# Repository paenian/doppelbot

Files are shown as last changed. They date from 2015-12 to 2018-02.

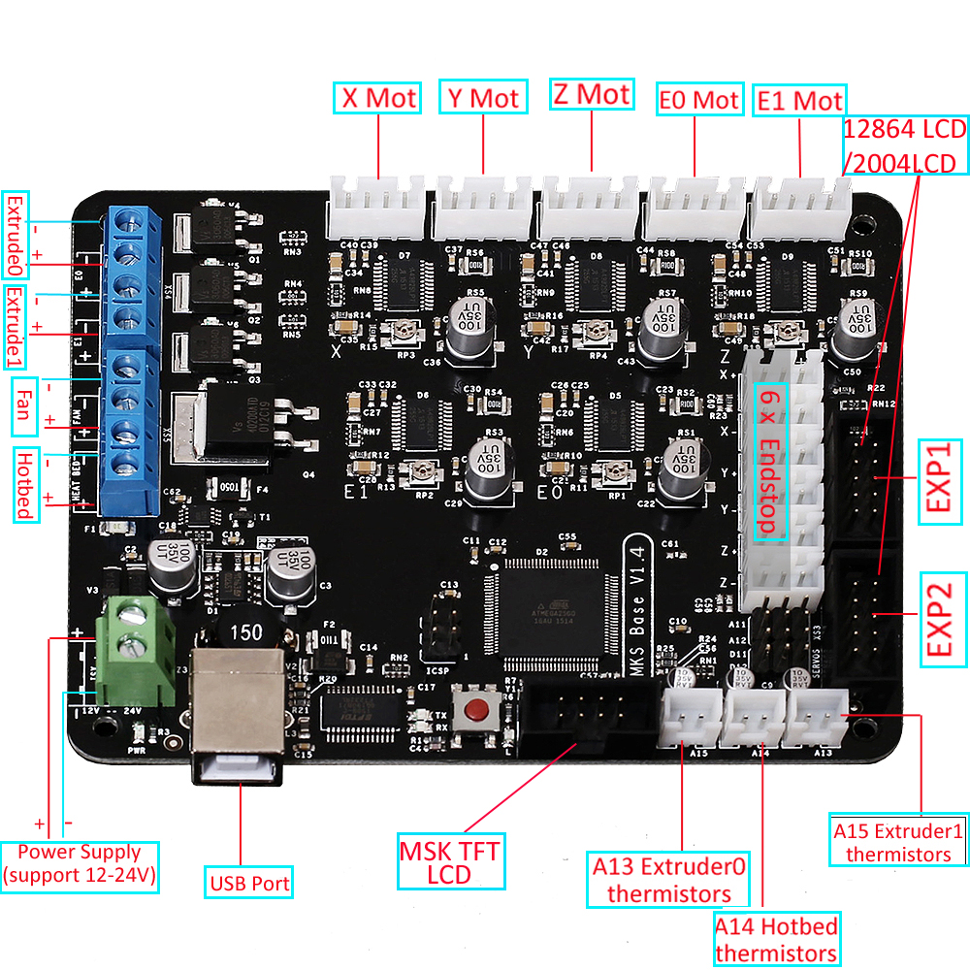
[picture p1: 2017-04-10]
unrelated/mks_base_schematic.jpg

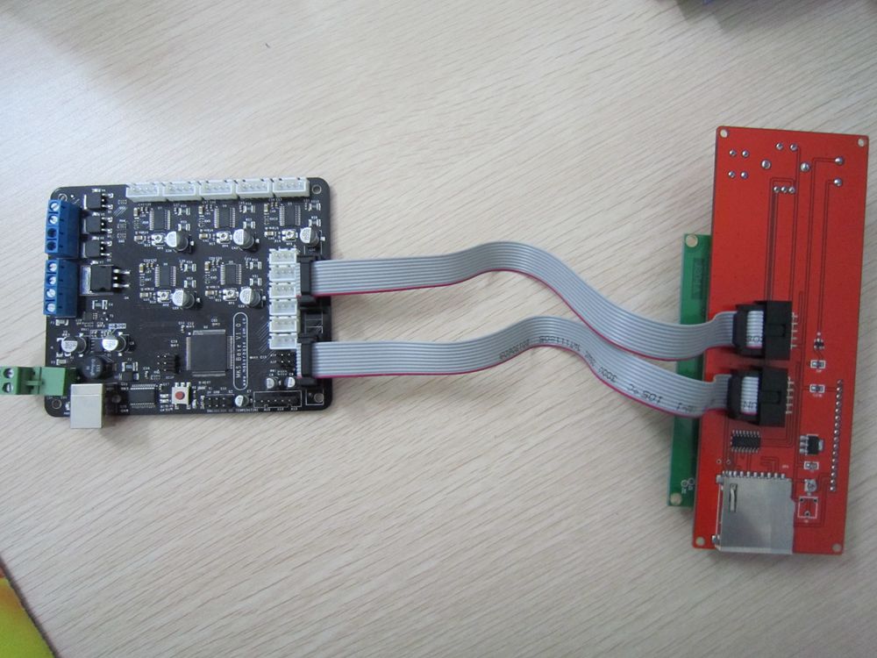
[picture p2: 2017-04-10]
unrelated/mks_base_lcd.jpg

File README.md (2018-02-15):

# doppelbot
Because I like designing 3d printers.

I made a deltabot, and it's really cool.  I can print really tall things.

But 3d prints are weakest in Z - printing really tall is maximizing the weak axis.

So instead of maximizing Z, I though about maximizing Y.  First concept here is the DoppelBot, which is a cube-shaped reprap that's easy to enclose, and has, by default, a one cubic foot build area. the print area of a standard reprap.  It accomplishes this 'twice as big' by the simple expedient of using two heated beds.

The basic design uses two lasercut endcaps, joined by OpenBuilds V-Rail.  The lasercut endcaps ensure that your rails are perfectly perpendicular and parallel - they don't even need to be cut to the exact correct length.  The machine itself uses a CoreXY gantry, and a Z bed with 3 independent leadscrews - so that the bed can truly level itself, none of this bed-level-compensation, if your bed is flat this machine will be able to tram it.

I'm experimenting with 9mm belts and over-built 3d printed carriages, to increase rigidity.

Also experimenting with a continous build system, wherein you can print dozens of objects in a row without human intervention.

Doppelbot running its first print
Picture of the Doppelbot Doppelbot!

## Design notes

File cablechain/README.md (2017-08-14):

# Cable Chain

Designed by Claghorn, this is a great printable cable chain for the Doppelbot.
https://www.thingiverse.com/thing:611593

You need 31 links, and two ends - probably make some custom ends eventually.

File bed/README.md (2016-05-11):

# doppelbot - Bed

## Frame
The bed is made of 2020 V-rail, although the V isn't used so feel free to use regular old 2020 extrusion.  In fact, that might be the default... it needs to be precisely cut, so you could simply order the exact lengths of 2020 from Misumi.

The beams will be joined by MDF endcaps, with MDF braces along the length.  The braces hold the beams square and true, as well as support the bed surface.  

The bed surface is borosilicate glass, a 1' by 2' piece.  Underneath that are two silicone heaters, and underneath those lie a sheet of welding blanket.  Securing the glass surface in place is done with binder clips - I know, it's not elegant, but they're cheap and effective.

It might be a good idea to add a thin piece of aluminum as a heat spreader... I'll certainly be looking into that.  Wondering if aluminum flashing would do it.

## Mechanical
The bed mechanics consist of three leadscrews secured on the end panels; two on the left (where the electronics et al live) and one on the left.  Eventually I would like to use one stepper driver per screw, to support true bed leveling; right now, though, they're just going to be linked to a single Z driver.

##MDF Parts
 - Encap: two needed
  - bed_end_top
  - bed_inside
  - bed_outside
 - Brace: two needed
  - bed_brace_top
  - 2 * bed_inside

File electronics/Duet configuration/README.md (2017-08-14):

# Duet Wifi Configuration!

This is the contents of my Duet Wifi SD card - it contains the latest non-beta firmware, 1.18.1, as well as the latest server, web control and wifi firmwares.
Firmware comes from here: https://github.com/dc42/RepRapFirmware/tree/dev/Release/Duet-WiFi/Stable
The rest of that GitHub is development et al - those are the latest stable bits.

## Firmwares
To update, copy this to your Duet Wifi SD card - as long as you have a working Duet Wifi firmware, it can update itself!

You need these four files in the /sys/ folder on your SD card:
DuetWebControl-1.15a.bin	Version 1.18	4 months ago
DuetWiFiFirmware-1.18.1.bin	Version 1.18.1	4 months ago
DuetWiFiServer-1.03-ch.bin	Version 1.16 release	9 months ago
iap4e.bin

Then you can run "M997 S0:1:2" to update all of them at once.
https://duet3d.com/wiki/Updating_more_than_one_firmware_at_a_time

## Config
Also in the /sys/ folder are the config files - here's a quick rundown.

All the configuration is done in gcode - so if you want to test a new config, simply send the gcode; if it works as you intended, you can then write it into the appropriate file.
Gcodes are documented here: http://reprap.org/wiki/Gcode
You MUST pay attention to the "supported by RepRapFirmware" box!

config.g - most of the parameters to set up the machine - steps per mm, extruder settings, endstops, etc.
homeall.g - what to do when G28 is called
home[xyz].g - what to do when G28 [XYZ] is called
pause.g - how to pause
resume.g - how to resume

I haven't looked at the rest of the .g files yet.

## Macros
I, uh, just copied these over.

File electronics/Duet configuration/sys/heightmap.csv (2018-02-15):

RepRapFirmware height map file v2 generated at 2018-00-27 00:49 | mean error 0.047 | deviation 0.098
xmin | xmax | ymin | ymax | radius | xspacing | yspacing | xnum | ynum
50.00 | 250.00 | 50.00 | 250.00 | -1.00 | 50.00 | 50.00 | 5 | 5
-0.064 | -0.031 | -0.071 | -0.072 | -0.061
0.036 | 0.132 | -0.082 | -0.001 | -0.007
0.069 | 0.301 | 0.227 | -0.106 | 0.054
0.110 | 0.147 | 0.064 | 0.087 | 0.021
0.150 | 0.064 | 0.016 | 0.079 | 0.113

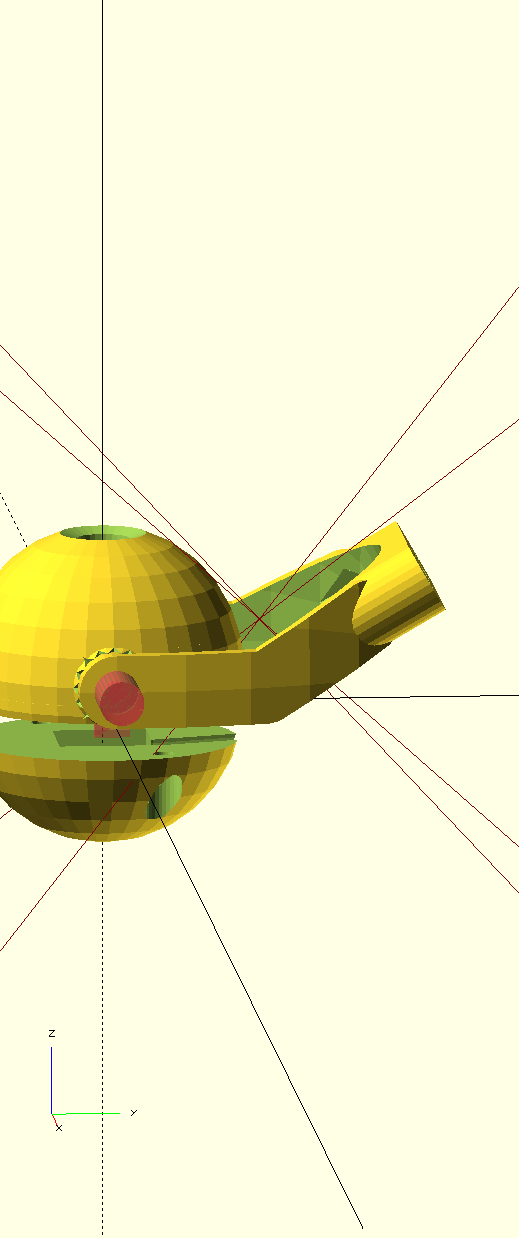
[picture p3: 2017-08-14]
unrelated/gurmeet/base_30.png

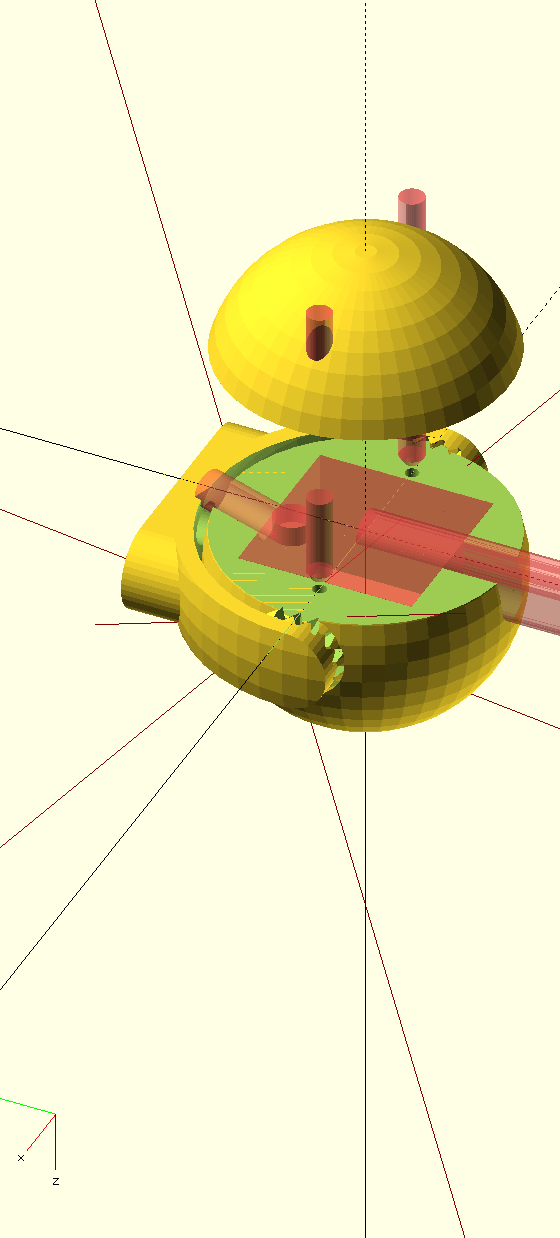
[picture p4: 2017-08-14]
unrelated/gurmeet/rear_view.png

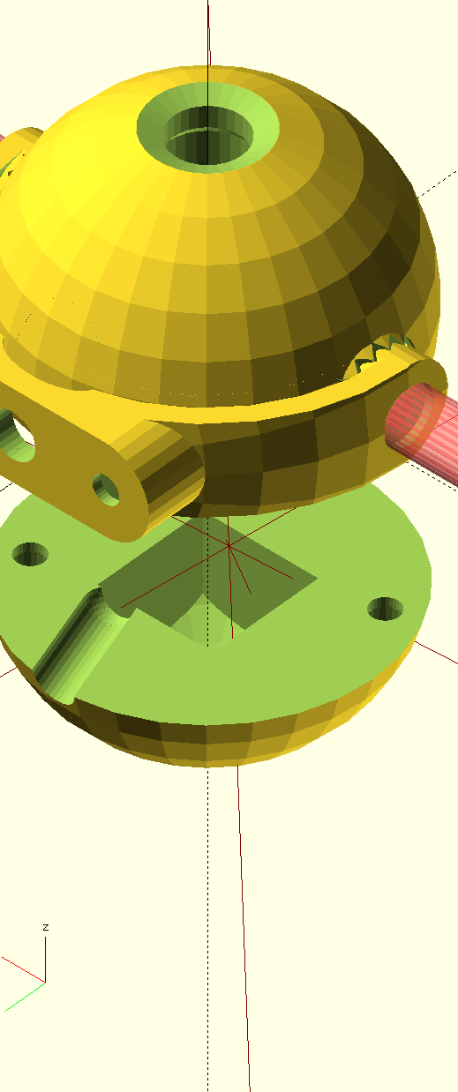
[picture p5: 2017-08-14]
unrelated/gurmeet/hole_pic.png

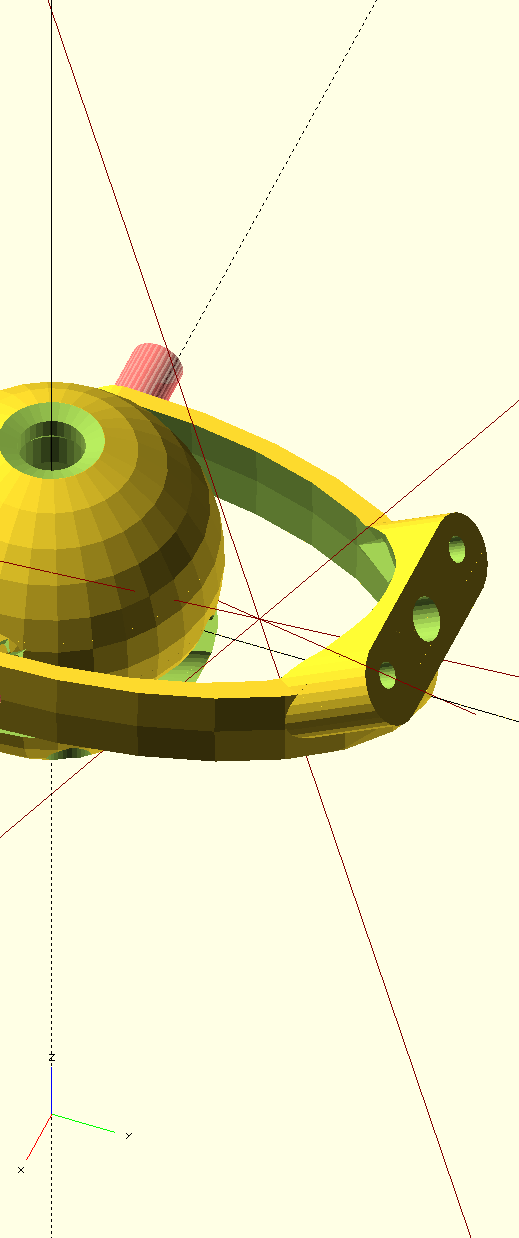
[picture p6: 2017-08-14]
unrelated/gurmeet/base_angle.png

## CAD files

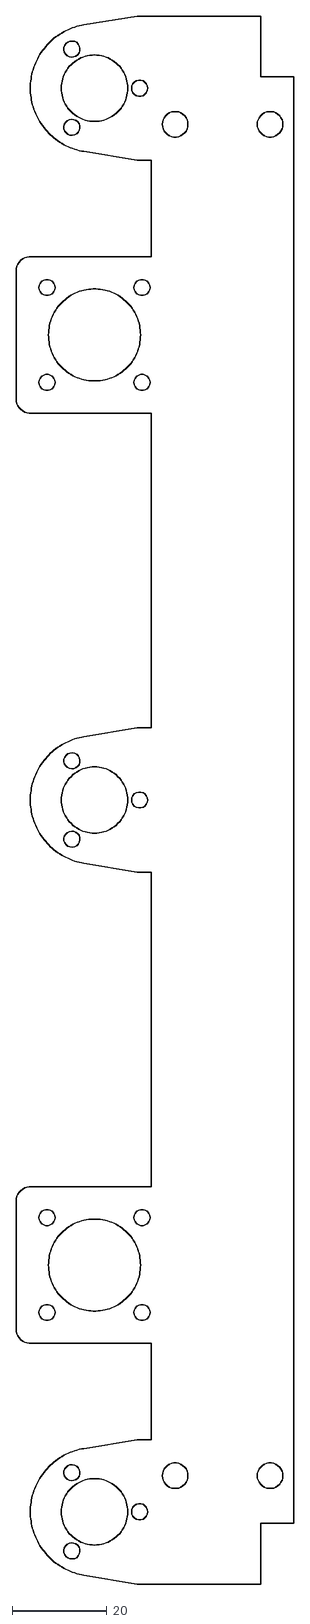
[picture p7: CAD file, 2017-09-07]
bed/dxf/bed_thick_top.dxf
58.5 x 330.4

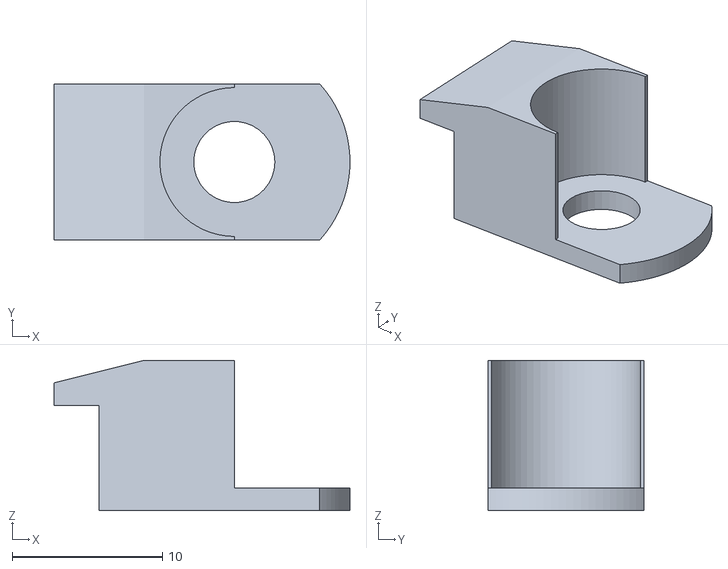
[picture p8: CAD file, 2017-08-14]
bed/stl/bed_clamp.stl
19.7 x 10.4 x 10.0

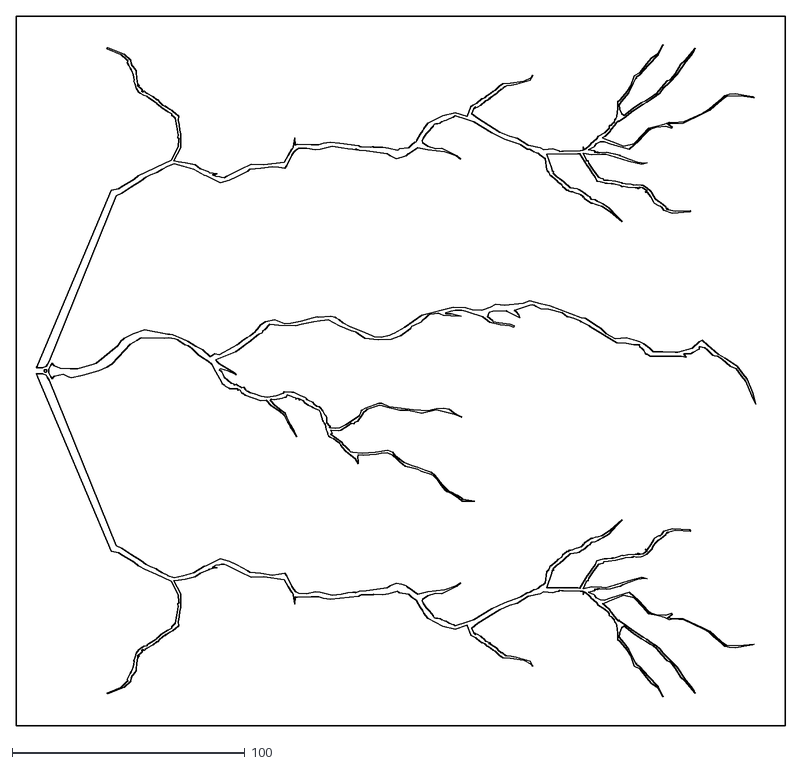
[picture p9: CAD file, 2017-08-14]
bed/vacuum_lightning.dxf
330.2 x 304.8

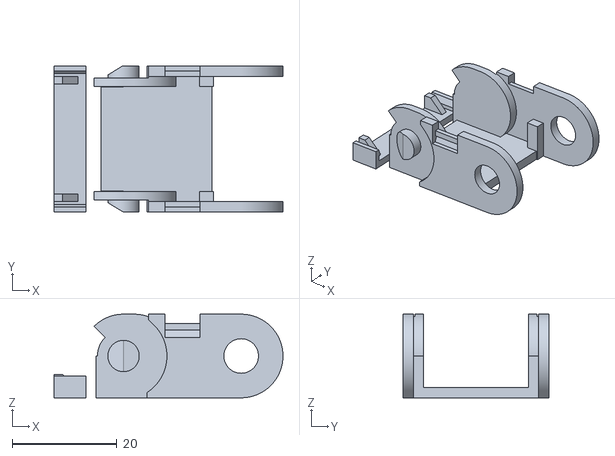
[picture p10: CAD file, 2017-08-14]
cablechain/schleppkette_thingiverse.stl
43.8 x 28.0 x 16.0

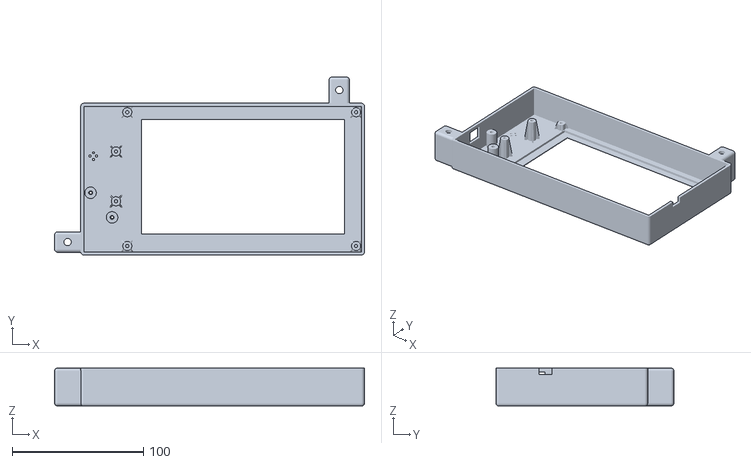
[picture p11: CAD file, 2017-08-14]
electronics/PanelDueEnclosure.stl
236.4 x 135.8 x 29.0

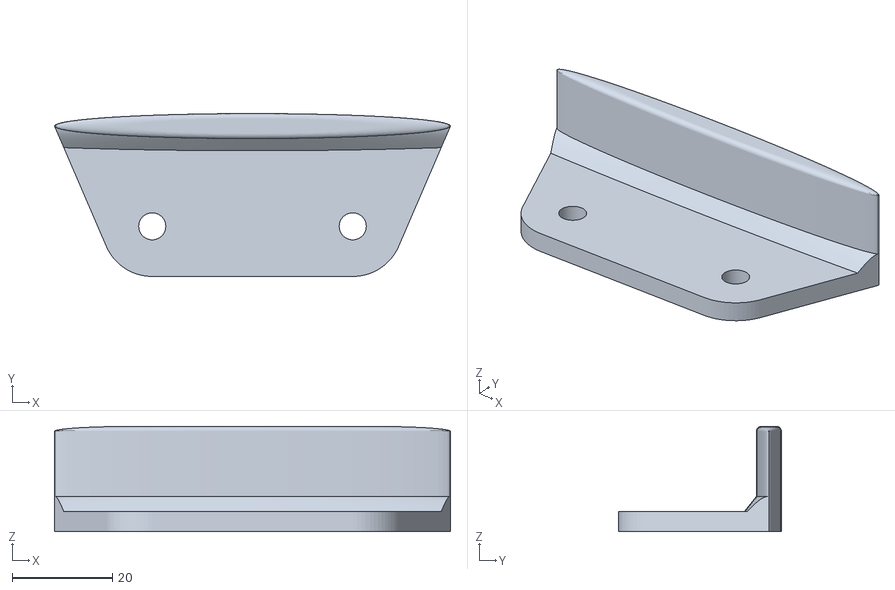
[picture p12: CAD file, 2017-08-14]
endcap/belt_separator.stl
79.0 x 32.5 x 21.0

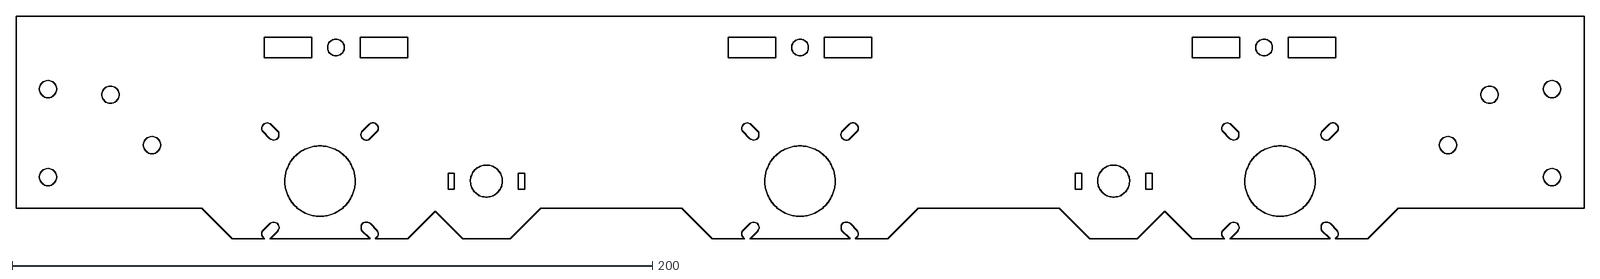
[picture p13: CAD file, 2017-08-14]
endcap/dxf/top_wall_plate_idler.dxf
490.0 x 69.5

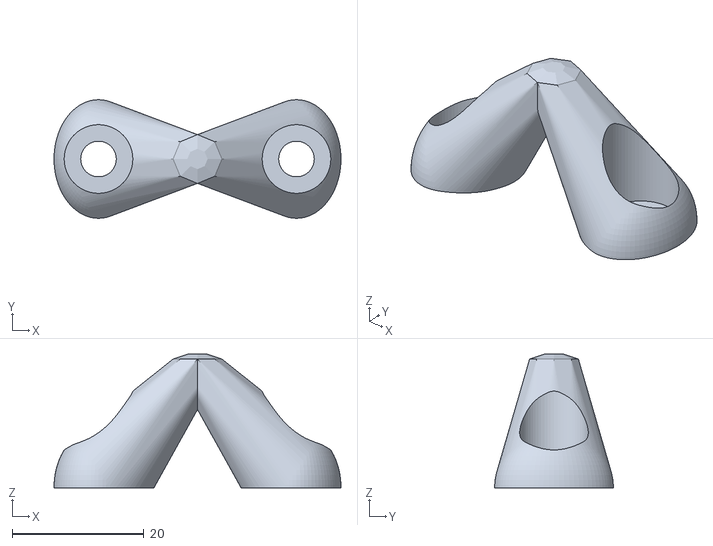
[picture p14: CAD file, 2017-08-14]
extras/feet.stl
43.5 x 18.0 x 20.2

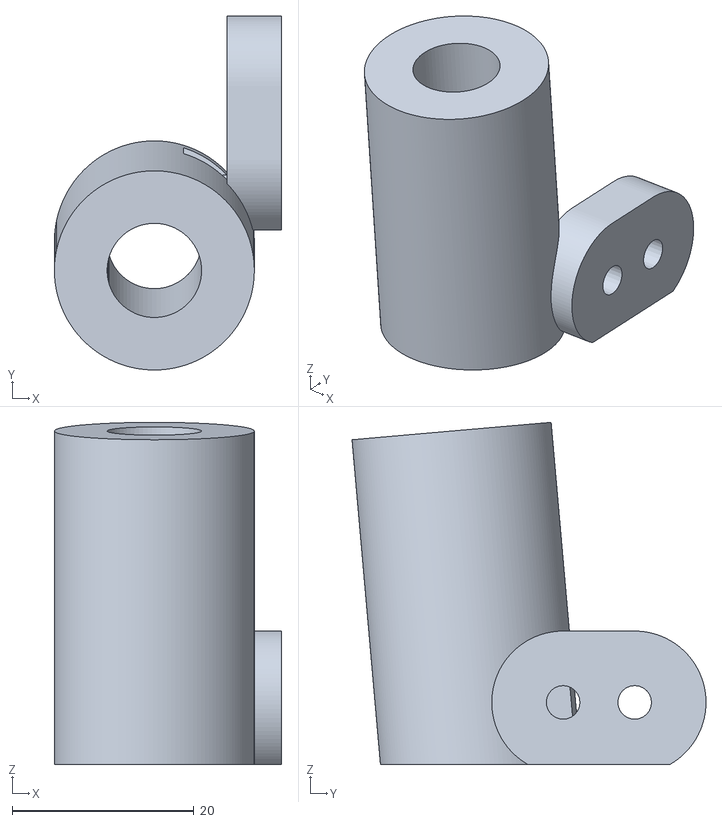
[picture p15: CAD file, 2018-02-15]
extruder/cablechain_mount.stl
25.0 x 39.0 x 37.7

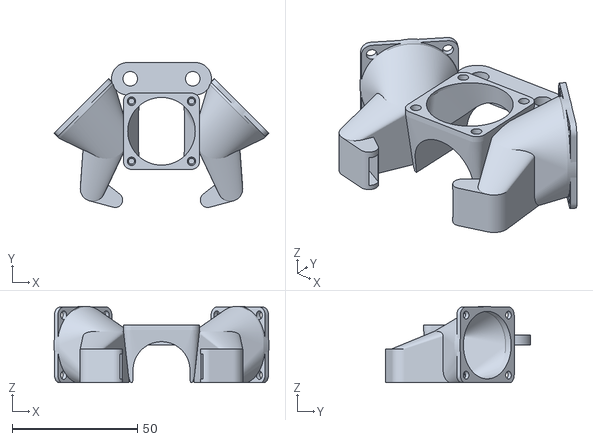
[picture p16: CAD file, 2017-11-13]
extruder/stl/cooling_fan_duct.stl
86.0 x 58.0 x 30.5

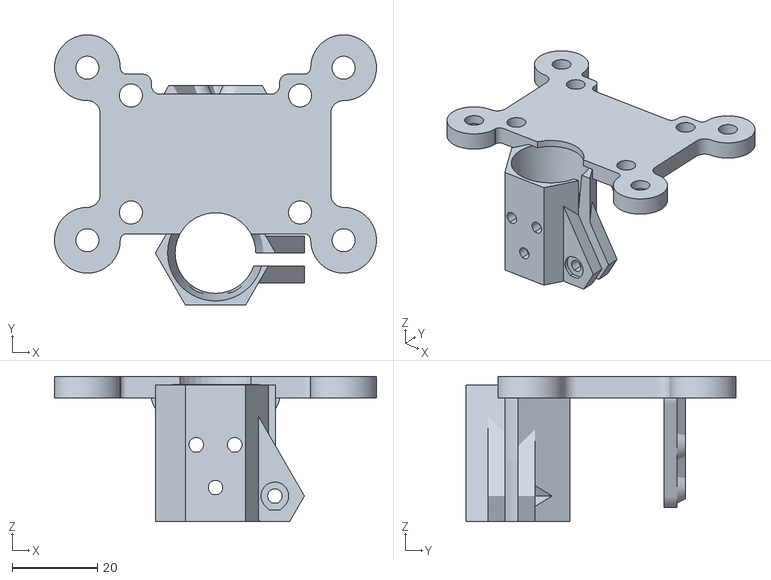
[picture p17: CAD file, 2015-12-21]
gantry.stl
75.4 x 63.3 x 34.0

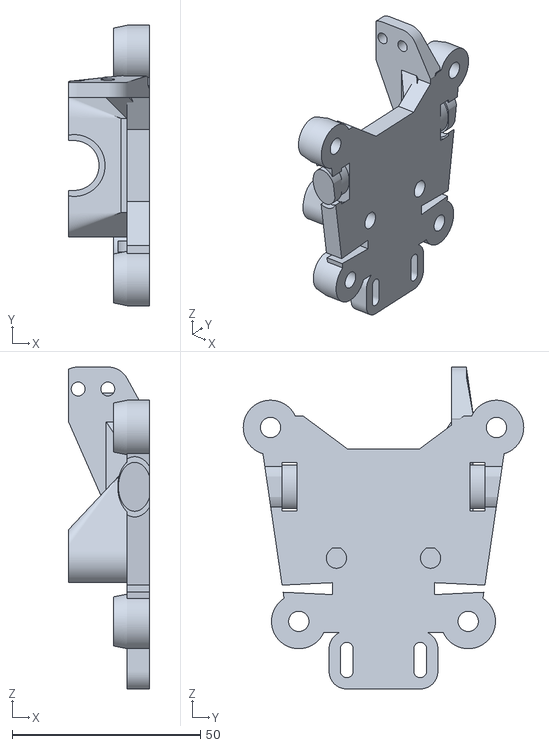
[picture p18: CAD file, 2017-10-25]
gantry/bowden_carriage.stl
21.5 x 74.5 x 85.5

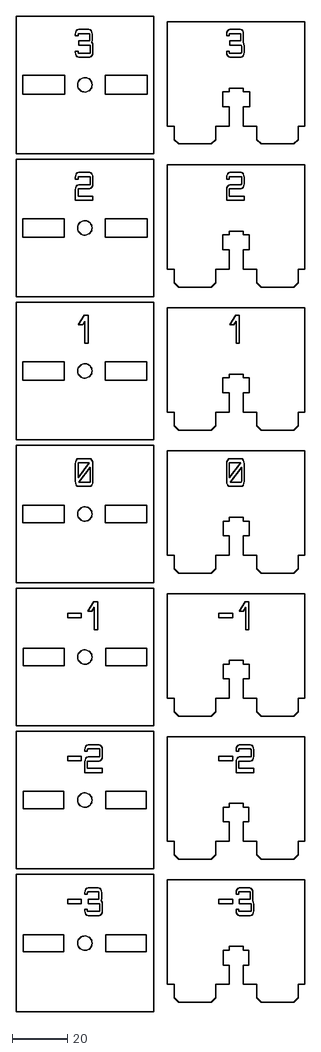
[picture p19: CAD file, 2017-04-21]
laser_testing/test_array.dxf
105.0 x 362.0

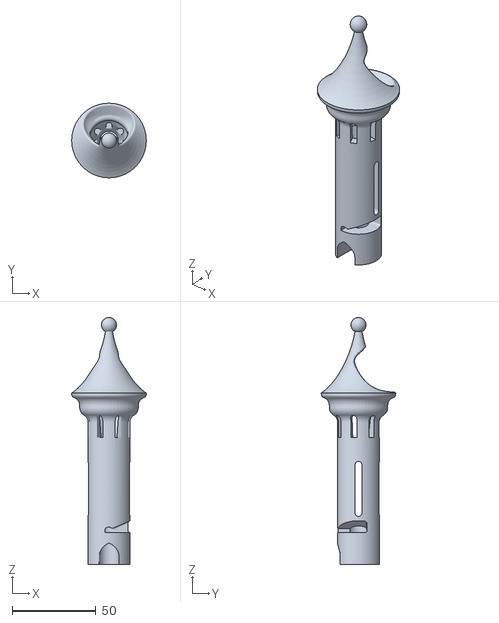
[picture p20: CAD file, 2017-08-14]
unrelated/castle_game/files-turm-klein.stl
44.6 x 44.6 x 147.6

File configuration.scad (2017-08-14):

in = 25.4;
mdf_wall = 6.5;
mdf_tab = 15;

wall = 5;

screw_slop = .2;
slop = .2;
laser_slop = -.1;

smooth_rod_rad = 10/2+laser_slop+.1;
smooth_rod_sep =490/5;

//this is for the old printer 
//smooth_rod_sep = 115;

//these can't change - measured values.
beam = 20;
bed_screw_sep = 309;
bed = 300;

layer_height=.2;

//this is using the gt2 idlers from robotdigg
//idler_rad = 13/2;
//idler_flange_rad = 18/2;
//idler_thick = 12;

//these use the smaller M5 flanged bearings as idlers
idler_rad = 16/2;
idler_flange_rad = 18/2;
idler_thick = 11.5;

//flanged bearing for the Z idler
z_bearing=22/2;
z_bearing_flange = 25/2;
leadscrew_rad = 8/2+slop;
leadscrew_shaft_rad = 7;
leadscrew_screw_rad = 19.05/2;

pulley_rad = 13/2;
pulley_flange_rad = 18/2;

//using the mini V-wheels
wheel_rad = 15.5/2;
wheel_inner_rad = 12.5/2;
wheel_clearance = 18;
wheel_height = 9;
wheel_inner_height = 5;
wheel_flange_rad = 16/2;

eccentric_rad = 7.3/2;
eccentric_flange_rad = 11/2;

//frame lengths - may be dependent on wall above.
frame_x = 500;  //we lose more in X because of the endcaps - it's where all the motors etc. will hide.
frame_y = 490;  //(490-300)/2-beam=75mm clearance on either side of the print bed.
corner_y = frame_y-75;
frame_z = 440;  //because the leadscrews are short, the motors stick up and the feet stick down
corner_z = frame_z-25;

corner_endplate = true; //this controls wether you want a full endcap, or just the corners.  Corners allows twisting in a direction that should be impossible when the rails are connected on both ends, but I wanted to retain the old option just in case.
corner_length = 170; //length of the corner side support.

foot_height = 25.4;  //extra meat on the legs

echo("BOM: 4, reg rail, 2020", frame_x, "Frame");

belt_thick = 9;
belt_width = 1.5;

//motor size and placement variables
motor_w = 42;
motor_r = 52/2;
motor_y = frame_y/2-beam-pulley_rad-belt_width; //distance motors are from the center.
motor_screw_sep = 31;




//gantry - might want to make it bigger
echo("BOM: 1, v-rail, 2020", frame_y, "Gantry");

//bed lengths
bed_x = 300+beam*2;
bed_y = 300;  //the screwholes on the bed should line up with the long_bed rails.

bed_screw_offset_y = bed_y/2;
bed_screw_offset_x = 15+5+2;

echo("BOM: 2, reg rail, 2020", bed_x, "Bed mount");
echo("BOM: 3, reg rail, 2020", bed_y, "Bed mount");  //might want more than three - to hold insulation well.

//standard screw variables
m3_nut_rad = 6.01/2+slop;
m3_nut_height = 2.4;
m3_rad = 3/2+slop;
m3_cap_rad = 3.25;
m3_cap_height = 2;
m3_sq_nut_rad = 7.9/2;


m4_nut_rad = 7.66/2+slop;
m4_nut_height = 3.2;
m4_rad = 4/2+slop;
m4_cap_rad = 7/2+slop;
m4_cap_height = 2.5;

m5_nut_rad = 8.79/2;
m5_sq_nut_rad = (8*sqrt(2)+slop/2)/2;
m5_nut_rad_laser = 8.79/2-.445;
m5_nut_height = 4.7;
m5_rad = 5/2+slop;
m5_rad_laser = 5/2-.1;
m5_cap_rad = 10/2+slop;
m5_cap_height = 3;
m5_washer_rad = 11/2+slop;


//redoing the frame with 10-24 screws - will use them for self-tapping screws
//on the endcaps, as well as all the MDF->MDF joints.  The reason for this is
//that the nuts on 10-24 are MUCH larger than  M5 nuts - making it way less
//likely to ruin the MDF.
ten24_rad = (.19*in/2+slop);
ten24_cap_rad = (.361*in/2+slop);
ten24_cap_height = .101*in+slop;
ten24_nut_rad = ((3/8*in)*cos(180/6))/2;
ten24_sq_nut_rad = ((3/8*in)*sqrt(2))/2+slop/2;

ten24_nut_height = 1/8*in+slop;

ten24_rad_laser = ten24_rad+laser_slop/2;
ten24_sq_nut_rad_laser = ten24_sq_nut_rad+laser_slop/2;
ten24_sq_nut_flat = 9.5;
ten24_sq_nut_flat_laser = ten24_sq_nut_flat+laser_slop;


echo(m5_sq_nut_rad);
echo(ten24_sq_nut_rad);



//some enums
MALE = 1;
FEMALE = -1;

//makes all the holes have lots of segments
$fs=.5;
$fa=.1;

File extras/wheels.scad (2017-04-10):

slop = .2;

m5_nut_rad = 8.79/2+slop;
m5_nut_height = 4.7;
m5_rad = 5/2+slop;
m5_dia = 5+slop;
m5_cap_rad = 9/2+slop;
m5_washer_rad = 11/2;

wall = 6;

//%cylinder(r=m8_washer_rad,h=20);
//%rotate([90,0,0])translate([-34.5,13,-2]) cylinder(r=m8_rad, h=30, center=true);

//the wheel
translate([-31,T/2,9]) rotate([90,0,0]) //this puts the wheel in the carrier
!wheel();

//the carrier
//rotated for printing
difference(){
	translate([0,0,17.5]) rotate([0,-12,0])
	carrier();
	translate([0,0,-50]) cube([100,100,100], center=true);
    
    translate([0,0,-18]) rotate([0,-24,0])
    translate([0,0,100]) cube([100,100,100], center=true);
}

module carrier(){
    bump_height = 1.5;
    
	thickness = wall+wall+bump_height*2+T;
	difference(){
		union(){
            //extra base clearance
            translate([6.25,0,0]) cube([6.5, 19.5, 39.5], center=true);
            
			hull(){
				cube([wall, thickness, 40], center=true);
				
				translate([-D/2-wall,0,0]) rotate([90,0,0]) cylinder(r=m5_washer_rad+wall, h=thickness, center=true);
			}
		}

		//mount the wheel
		translate([-D/2-wall,0,0]) rotate([-90,0,0]) {
			rotate([0,0,25]) cap_cylinder(r=m5_rad, h=50, center=true);
			difference(){
				scale([1,1.25,1]) intersection(){
					cylinder(r=D/2+wall,h=T+2,center=true,$fn=100);
					scale([1,1,.5]) sphere(r=D/2+wall, $fn=90);
				}
                
				//bumps to hold the wheel centered
				for(i=[0,1]) mirror([0,0,i]) translate([0,0,-T/2-1.1]) cylinder(r1=m5_washer_rad+1, r2=m5_washer_rad-1, h=bump_height);
			}
		}
		
		//bolt indent
		translate([-D/2-wall,0,0])rotate([-90,0,0]) translate([0,0,-T/2-1.05-wall]) cylinder(r=m5_washer_rad+.25, h=2);
		//nut indent
		mirror([0,1,0]) translate([-D/2-wall,0,0])rotate([-90,0,0]) translate([0,0,-T/2-1.05-wall]) cylinder(r=m5_nut_rad+.1, h=2, $fn=6);

		//mount the carrier
		for(i=[-10,10]) translate([0,0,i]) rotate([0,90,0]){
			rotate([0,0,-90]) cap_cylinder(r=m5_rad, h=30, center=true);
			translate([0,0,-30]) rotate([0,0,-90]) cap_cylinder(r=m5_cap_rad+.25, h=35);
		}
	}
}

// outer diameter of ring
D=65;
// thickness
T=18;
// clearance
tol=.3;
number_of_planets=8;
number_of_teeth_on_planets=6;
approximate_number_of_teeth_on_sun=13;
// pressure angle
P=40;//[30:60]
// number of teeth to twist across
nTwist=1;
// width of center hole
w=m5_dia+1  ;

DR=0.5*1;// maximum depth ratio of teeth

m=round(number_of_planets);
np=round(number_of_teeth_on_planets);
ns1=approximate_number_of_teeth_on_sun;
k1=round(2/m*(ns1+np));
k= k1*m%2!=0 ? k1+1 : k1;
ns=k*m/2-np;
echo(ns);
nr=ns+2*np;
pitchD=0.9*D/(1+min(PI/(2*nr*tan(P)),PI*DR/nr));
pitch=pitchD*PI/nr;
echo(pitch);
helix_angle=atan(2*nTwist*pitch/T);
echo(helix_angle);

phi=$t*360/m;
module wheel(){
	translate([0,0,T/2]){
		difference(){
			intersection(){
				cylinder(r=D/2+1,h=T,center=true,$fn=100);
				scale([1,1,1.25]) sphere(r=D/2+1, $fn=90);
			}
			render() herringbone(nr,pitch,P,DR,-tol,helix_angle,T+0.2);
		}
		rotate([0,0,(np+1)*180/ns+phi*(ns+np)*2/ns])
		difference(){
			mirror([0,1,0])
				render() herringbone(ns,pitch,P,DR,tol,helix_angle,T);
			cylinder(r=w/2,h=T+1,center=true);
		}
		for(i=[1:m])rotate([0,0,i*360/m+phi])translate([pitchD/2*(ns+np)/nr,0,0])
			render() rotate([0,0,i*ns/m*360/np-phi*(ns+np)/np-phi])
				herringbone(np,pitch,P,DR,tol,helix_angle,T);
	}
}

module rack(
	number_of_teeth=15,
	circular_pitch=10,
	pressure_angle=28,
	helix_angle=0,
	clearance=0,
	gear_thickness=5,
	flat=false){
addendum=circular_pitch/(4*tan(pressure_angle));

flat_extrude(h=gear_thickness,flat=flat)translate([0,-clearance*cos(pressure_angle)/2])
	union(){
		translate([0,-0.5-addendum])square([number_of_teeth*circular_pitch,1],center=true);
		for(i=[1:number_of_teeth])
			translate([circular_pitch*(i-number_of_teeth/2-0.5),0])
			polygon(points=[[-circular_pitch/2,-addendum],[circular_pitch/2,-addendum],[0,addendum]]);
	}
}

module herringbone(
	number_of_teeth=15,
	circular_pitch=10,
	pressure_angle=28,
	depth_ratio=1,
	clearance=0,
	helix_angle=0,
	gear_thickness=5){
union(){
	gear(number_of_teeth,
		circular_pitch,
		pressure_angle,
		depth_ratio,
		clearance,
		helix_angle,
		gear_thickness/2);
	mirror([0,0,1])
		gear(number_of_teeth,
			circular_pitch,
			pressure_angle,
			depth_ratio,
			clearance,
			helix_angle,
			gear_thickness/2);
}}

module gear (
	number_of_teeth=15,
	circular_pitch=10,
	pressure_angle=28,
	depth_ratio=1,
	clearance=0,
	helix_angle=0,
	gear_thickness=5,
	flat=false){
pitch_radius = number_of_teeth*circular_pitch/(2*PI);
twist=tan(helix_angle)*gear_thickness/pitch_radius*180/PI;

flat_extrude(h=gear_thickness,twist=twist,flat=flat)
	gear2D (
		number_of_teeth,
		circular_pitch,
		pressure_angle,
		depth_ratio,
		clearance);
}

module flat_extrude(h,twist,flat){
	if(flat==false)
		linear_extrude(height=h,twist=twist,slices=twist/6)child(0);
	else
		child(0);
}

module gear2D (
	number_of_teeth,
	circular_pitch,
	pressure_angle,
	depth_ratio,
	clearance){
pitch_radius = number_of_teeth*circular_pitch/(2*PI);
base_radius = pitch_radius*cos(pressure_angle);
depth=circular_pitch/(2*tan(pressure_angle));
outer_radius = clearance<0 ? pitch_radius+depth/2-clearance : pitch_radius+depth/2;
root_radius1 = pitch_radius-depth/2-clearance/2;
root_radius = (clearance<0 && root_radius1<base_radius) ? base_radius : root_radius1;
backlash_angle = clearance/(pitch_radius*cos(pressure_angle)) * 180 / PI;
half_thick_angle = 90/number_of_teeth - backlash_angle/2;
pitch_point = involute (base_radius, involute_intersect_angle (base_radius, pitch_radius));
pitch_angle = atan2 (pitch_point[1], pitch_point[0]);
min_radius = max (base_radius,root_radius);

intersection(){
	rotate(90/number_of_teeth)
		circle($fn=number_of_teeth*3,r=pitch_radius+depth_ratio*circular_pitch/2-clearance/2);
	union(){
		rotate(90/number_of_teeth)
			circle($fn=number_of_teeth*2,r=max(root_radius,pitch_radius-depth_ratio*circular_pitch/2-clearance/2));
		for (i = [1:number_of_teeth])rotate(i*360/number_of_teeth){
			halftooth (
				pitch_angle,
				base_radius,
				min_radius,
				outer_radius,
				half_thick_angle);		
			mirror([0,1])halftooth (
				pitch_angle,
				base_radius,
				min_radius,
				outer_radius,
				half_thick_angle);
		}
	}
}}

module halftooth (
	pitch_angle,
	base_radius,
	min_radius,
	outer_radius,
	half_thick_angle){
index=[0,1,2,3,4,5];
start_angle = max(involute_intersect_angle (base_radius, min_radius)-5,0);
stop_angle = involute_intersect_angle (base_radius, outer_radius);
angle=index*(stop_angle-start_angle)/index[len(index)-1];
p=[[0,0],
	involute(base_radius,angle[0]+start_angle),
	involute(base_radius,angle[1]+start_angle),
	involute(base_radius,angle[2]+start_angle),
	involute(base_radius,angle[3]+start_angle),
	involute(base_radius,angle[4]+start_angle),
	involute(base_radius,angle[5]+start_angle)];

difference(){
	rotate(-pitch_angle-half_thick_angle)polygon(points=p);
	square(2*outer_radius);
}}

// Mathematical Functions
//===============

// Finds the angle of the involute about the base radius at the given distance (radius) from it's center.
//source: http://www.mathhelpforum.com/math-help/geometry/136011-circle-involute-solving-y-any-given-x.html

function involute_intersect_angle (base_radius, radius) = sqrt (pow (radius/base_radius, 2) - 1) * 180 / PI;

// Calculate the involute position for a given base radius and involute angle.

function involute (base_radius, involute_angle) =
[
	base_radius*(cos (involute_angle) + involute_angle*PI/180*sin (involute_angle)),
	base_radius*(sin (involute_angle) - involute_angle*PI/180*cos (involute_angle))
];

module cap_cylinder(r=1, h=1, center=false){
	render() union() {
		cylinder(r=r, h=h, center=center);
		intersection(){
			rotate([0,0,22.5]) cylinder(r=r/cos(180/8), h=h, $fn=8, center=center);
			translate([0,-r/cos(180/4),0]) rotate([0,0,0]) cylinder(r=r/cos(180/4), h=h, $fn=4, center=center);
		}
	}
}

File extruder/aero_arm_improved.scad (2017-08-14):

tol = .2;

m5_rad = 5/2+tol;

%cylinder(r=2.5, h=13, $fn=64, center=true);
printable_arm();
translate([-11,0,0]) idler_support_washer();
translate([-13.5,12,0]) rotate([0,0,-45]) shaft_support_insert(thick = 2);

//draw in place
%translate([idler_offset_x, idler_offset_y, 0]) rotate([0,0,180]) mirror([0,0,1]) idler_support_washer();
%translate([0, 0, -2.05]) rotate([0,0,180]) shaft_support_insert(thick = 2);

arm_thick = 8;
arm_width = 10;
arm_length = 40;

idler_offset_y = 16;
idler_offset_x = -5.5;

filament_guide_offset_x = -11;
filament_guide_rad = 4/2;
filament_guide_length = 18;
filament_rad = 1.75/2+tol;

nub_rad = 4/2-tol/2;
nub_offset_x = 3;
nub_offset_y = 23;

//bearing size for the motor shaft
bearing_rad = 10/2+tol/2;
bearing_thick = 4;
bearing_inner_rad = 8/2+tol;
bearing_washer_thick = .5;
bearing_bore = 5/2-tol/2;

$fn = 64;

//this is a version of the arm that's filled in & toleranced for easier printing
module printable_arm(){
    wall = 2;
    min_rad = .5;
    %rotate([0,180,0]) orig_arm();
    difference(){
        union(){
            //main body
            translate([0,arm_length/2,0]) minkowski(){
                union(){
                    //arm
                    cube([arm_width-min_rad*2, arm_length-min_rad*2, arm_thick-min_rad*2], center=true);
                    //filament guide
                    translate([filament_guide_offset_x,arm_length/2-filament_guide_length/2,0]) cube([filament_guide_rad*2+wall*2,filament_guide_length-min_rad*2,arm_thick-min_rad*2], center=true);
                    //connect them a bit better
                    translate([filament_guide_offset_x/2,arm_length/2-filament_guide_length/2,0]) cube([filament_guide_rad*2+wall*2,filament_guide_length-min_rad*4,arm_thick/2-min_rad*2], center=true);
                }
                sphere(r=.5, $fn=12);
            }
            
            //bearing meat
            cylinder(r=bearing_rad+wall, h=arm_thick, center=true);
            
            //idler meat
            intersection(){
                translate([idler_offset_x, idler_offset_y]) cylinder(r=bearing_rad+wall, h=arm_thick, center=true);
                cube([arm_width+wall*3,100,arm_thick], center=true);
            }
            
            //nubbin - really not useful, the nub clear out overwrites it.
            translate([nub_offset_x, nub_offset_y, 0]) sphere(r=nub_rad);
        }
        /////////////////////CUTOUTS
        
        
        
        //filament guide hole - this is for a teflon tube
        translate([0,arm_length/2+wall,0]){
            //tube hole
            translate([filament_guide_offset_x,arm_length/2-filament_guide_length/2,0]) rotate([90,0,0]) cylinder(r=filament_guide_rad, h=filament_guide_length, center=true);
            //slit on top, to make sure the tube is in
            translate([filament_guide_offset_x,arm_length/2-filament_guide_length/2-wall/2,arm_thick/2]) cube([wall/2,filament_guide_length+1,arm_thick], center=true);
            
            //filament hole
            translate([filament_guide_offset_x,0,0]) rotate([90,0,0]) cylinder(r=filament_rad, h=arm_length, center=true);
        }
        
        //bearing mount on the motor shaft
        translate([0,0,-bearing_thick/2+arm_thick/2]) cylinder(r=bearing_rad, h=bearing_thick+.1, center=true, $fn=64);
        cylinder(r=bearing_inner_rad, h=arm_thick+1, center=true, $fn=64);
        //this cuts out a bottom corner so that it misses the hotend holder.  Probably glue the bearing in, but really there's nowhere for it to go.
        translate([-bearing_rad,-bearing_rad,0]) cube([bearing_rad*2, bearing_rad*2, arm_thick+2], center=true);
        
        //idler mount
        translate([idler_offset_x, idler_offset_y])
        difference(){
            hull() {
                cylinder(r=bearing_rad+.5, h=bearing_thick+bearing_washer_thick*2, center=true);
                translate([0,0,arm_thick]) cylinder(r=bearing_rad+.75, h=bearing_thick, center=true);
            }
            
            //bottom washer
            translate([0,0,-bearing_thick/2-bearing_washer_thick-.1]) cylinder(r1=bearing_rad, r2=bearing_inner_rad-1, h=bearing_washer_thick+.1);
            //shaft
            cylinder(r1=bearing_bore, r2=bearing_bore-tol/2, h=arm_thick, center=true);
        }//end idler mount
        
        //nubbin - really not useful, the nub clear out overwrites it.
        difference(){
            translate([arm_width/2, nub_offset_y+wall-.25, 0]) hull(){
                cube([(arm_width/2-nub_offset_x)*2+1,10,arm_thick+1], center=true);
                translate([arm_width,0,0]) cube([(arm_width/2-nub_offset_x)*2+1,15,arm_thick+1], center=true);
            }
            
            hull(){
                translate([nub_offset_x, nub_offset_y, 0]) sphere(r=nub_rad);
                translate([0, nub_offset_y, 0]) sphere(r=nub_rad+.5);
            }
        }
    }
}

module idler_support_washer(){
    difference(){
        union(){
            translate([0,0,-arm_thick/2]) cylinder(r=bearing_rad+.75-tol, h=1.45);
            //washer
            translate([0,0,-bearing_thick/2-bearing_washer_thick-.1]) cylinder(r1=bearing_rad-tol, r2=bearing_inner_rad-1, h=bearing_washer_thick+.1);
        }
        
        cylinder(r1=bearing_bore+tol/2, r2=bearing_bore+tol, h=arm_thick+.1, center=true);
        
        //flat to miss the inside of the hotend mount
        translate([bearing_rad*2-2,0,0]) cube([bearing_rad*2, 20, arm_thick+1], center=true);
    }    
}

module shaft_support_insert(thick = 2){
    translate([0,0,-arm_thick/2])

    union(){
        difference(){
            //the base
            cylinder(r=bearing_inner_rad+2, h=thick);
            //missing a chunk for the hotend mount clearance
            translate([bearing_inner_rad+2,bearing_inner_rad+2,0]) cylinder(r=bearing_inner_rad+2, h=thick*4, center=true);
        }
        cylinder(r1=bearing_inner_rad-tol*1.5, r2=bearing_inner_rad-tol*2, h=thick+arm_thick/2-1);
    }
}

//this is the original arm, oriented
module orig_arm(){
    rotate([0,180,0]) translate([6.666,-23,13.5])
    rotate([0,0,180]) import("aero_arm.stl");
}

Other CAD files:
unrelated/gurmeet/clamp.stl
unrelated/tetrahedron.dxf
Writescad/Letters.dxf
bed/dxf/bed_double_end_top.dxf
extruder/motor_mount.scad
Writescad/BlackRose.dxf
Writescad/braille.dxf
Writescad/knewave.dxf
Writescad/orbitron.dxf
Writescad/write.scad
beam.scad
bed/bed.scad
bed/dxf/bed_brace_top.dxf
bed/dxf/bed_end_support.dxf
bed/dxf/bed_inside_support.dxf
bed/dxf/bed_long_clamp.stl
bed/dxf/bed_single_end_top.dxf
cablechain/CableChain.stl
cablechain/end_two.scad
cablechain/end_two.stl
cablechain/new-chain.scad
cablechain/nobar_sixteen.scad
cablechain/nobar_sixteen.stl
cablechain/schleppkette_thingiverse.scad
cablechain/spring_sixteen.scad
cablechain/spring_sixteen.stl
connectors.scad
corner.scad
corner.stl
corner_XYZ.stl
corner_XYz.stl
corner_XyZ.stl
corner_Xyz.stl
corner_xYZ.stl
corner_xYz.stl
corner_xyZ.stl
corner_xyz.stl
drill_plate.scad
electronics/PanelDueEnclosure.scad
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

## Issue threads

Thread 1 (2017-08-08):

Build integrated Gantry Extruder

paenian, 2017-08-08:
The extruder attached to the gantry is cumbersome, and needs work - it'd be easier and stronger to create an extruder that's mounted directly to the gantry.

Ideally, several extruders, such that they can be swapped out with minimal time.

1) tensioner needs to be moved to the rear gantry.
2) belt should snap over/onto the front gantry, with some sort of clip to hold it in place.
3) Aero can be mounted motor-to-the-rail

paenian, 2017-08-11:
Built!

Closed 2017-08-11.

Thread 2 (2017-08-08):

double tensioners on rear gantry

paenian, 2017-08-08:
Angle the belt tensioner in order to add another tensioner for the other half of the belt - cross-tensioning.

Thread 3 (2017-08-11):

Create a wiper

paenian, 2017-08-11:
To clean off the nozzle before every print - maybe a stiff brush?  Wiper should be easily replaceable.

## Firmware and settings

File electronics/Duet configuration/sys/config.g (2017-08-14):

; CoreXY config file for 300x300x300mm doppelbot

M111 S0				; Debug off
M550 PBoxxyBrown		; Machine name (can be anything you like)
M551 Preprap			; Machine password (used for FTP connections)
ns)

;*** If you have more than one Duet on your network, they must all have different MAC addresses, so change the last digits
M540 P0xBE:0xEF:0xDE:0xAD:0xFE:0xED ; MAC Address

;*** Wifi Networking
M552 S1				; Enable WiFi

M555 P2				; Set output to look like Marlin
M575 P1 B57600 S1		; Comms parameters for PanelDue

; Machine configuration
M569 P0 S0			; Drive 0 goes forwards (change to S0 to reverse it)
M569 P1 S0			; Drive 1 goes forwards
M569 P2 S1			; Drive 2 goes forwards
M569 P3 S1			; Drive 3 goes forwards
M569 P4 S1			; Drive 4 goes forwards

; If you use an endstop switch for Z homing, change Z0 to Z1 in the following line, and see also M558 command later in this file
M574 X1 Y1 Z0 S1					; set endstop configuration (X and Y and endstops only, at low end, active high)

M667 S1							; set CoreXY mode

M350 X16 Y16 E16 I1    					; Set 16x microstepping with interpolation
M92 X80 Y80 Z1600					; Set axis steps/mm
M92 E419:419						; Set extruder steps/mm
M906 X1000 Y1000 Z1000 E1000	; Set motor currents (mA)
M201 X1000 Y1000 Z15 E1000	; Accelerations (mm/s^2)
M203 X15000 Y15000 Z100 E3600	; Maximum speeds (mm/min)
M566 X600 Y600 Z30 E20		; Maximum jerk speeds mm/minute
M208 X300 Y300 Z300		; set axis maxima (adjust to suit your machine)
M208 X-8 Y0 Z-0.5 S1		; set axis minima (adjust to make X=0 and Y=0 the edges of the bed)
G21				; Work in millimetres
G90				; Send absolute coordinates...
M83				; ...but relative extruder moves

; Z probe
M558 P1 X0 Y0 Z1                    ; Analog Z probe, also used for homing the Z axis
G31 Z1.30 P500                      ; Set the probe height and threshold (put your own values here)

; The following M557 commands are not needed if you are using a bed.g file to perform bed compensation
;*** Adjust the XY coordinates in the following M557 commands to suit your build and the position of the Z probe
M557 P0 X50 Y50                      ; Four... 
M557 P1 X50 Y250                    ; ...probe points...
M557 P2 X250 Y250                   ; ...for bed...
M557 P3 X250 Y50                     ; ...levelling
;M557 P4 X141 Y82.5                 ; 5th probe point for levelling

; Thermistors and heaters
;*** You can use S and B parameters to define the parameters of the thermistors you are using
M305 P0 R4700 H0 L0					; Put your own H and/or L values here to set the bed thermistor ADC correction
M305 P1 R4700 H0 L0					; Put your own H and/or L values here to set the first nozzle thermistor ADC correction
M305 P2 R4700 H0 L0					; Put your own H and/or L values here to set the second nozzle thermistor ADC correction
M301 H1 P10 I0.10 D100 T0.50 S1.0	; PID settings for extruder 0
M301 H2 P10 I0.10 D100 T0.50 S1.0	; PID settings for extruder 1
M570 S120							; Increase to allow extra heating time if needed

; Tool definition
M563 P0 D0 H1                       ; Define tool 0
G10 P0 S0 R0                        ; Set tool 0 operating and standby temperatures

;*** If you have a dual-nozzle build, un-comment the following 3 lines
;M563 P1 D1 H2                      ; Define tool 1
;G10 P1 S0 R0                       ; Set tool 1 operating and standby temperatures

;*** If you are using axis compensation, put the figures in the following command
M556 S78 X0 Y0 Z0                   ; Axis compensation here
T0									; select first hot end

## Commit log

2015-08-08 Made the first corner :-)
    The corner has one beam inside of it, and the other two hanging off. The inside beam must be installed LAST.
    [configuration.scad, corner.scad, corner.stl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]
2015-08-17 Frame's done :-)
    The beam measurements are approximate for now - have to look up the real ones and fix.
    [assembled.scad, beam.scad, configuration.scad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]
2015-09-16 Making a 2040 corner.
    The three ghosted extrusions are in the right spot - the extra, unused tab will be for mounting motors and/or idler pulleys.
    [beam.scad, configuration.scad, corner.scad]
2015-09-16 Updated corner for 2040 extrusion
    2020 wasn't strong enough.
    Also added motor mount to the corner.
    TODO:
    add idler mounts to the corner - at which point, frame will be complete.
    [configuration.scad, corner.scad, corner.stl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]
2015-09-16 Added the idler corner.
    The machine has two motor corners and two idler corners, and four
    unadorned corners for the base.
    I'll probably add a little foot to the base corners for good measure,
    but these are ready to go for now.
    [corner.scad]
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2015-10-27 Minor updates, start work on gantry
    Still figuring out where belts can go... I'd like them to be hidden
    inside the frame, but it'd be simpler to put 'em up top... maybe stick
    the motor out as well? Otherwise we'd need a couple extra idlers.
    [corner.scad, functions.scad]
2015-11-03 Updated corners, to route the belt around the beam
    Should have just enough clearance now. Next step is to design the beam
    :100:
    [configuration.scad, corner.scad]
2015-11-17 Starting work on the gantry.
    The gantry and gantry ends are the next big pieces. After that, the Z
    axis needs to be developed.
    [configuration.scad, corner.scad, gantry.scad]
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2015-11-18 First stab at the x gantry. e3d cyclops on one side, induction sensor on the other.
    Outer holes are the v-wheels, inner wheels are just M5 screws to grab each end of the belt. There should be a tensioning solution at some point... but not now.
    [gantry.scad, gantry.stl]
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2015-11-20 Had to embiggen all the m5 holes, in order to use the dome-head screws.
    [configuration.scad, corner.scad, corner_XYZ.stl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]
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2015-12-21 Created the gantry ends, updated the gantry
    And that's all the parts! Printing and testing.
    [configuration.scad, corner.scad, gantry.scad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]
2016-01-02 Fixed up the corners, cleaning mostly
    [assembled.scad, beam.scad, corner.stl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]
2016-03-17 Moved the printed corners... trying my hand at a large lasercut panel.
    Plan is for a torsion box on each end, with a 2040 frame connecting them.
    Angling for a 300mm square bed, expandable to 300x600 for the next go-round.
    Paul
    [assembled.scad, configuration.scad, connectors.scad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]
2016-03-19 threw up some end plates
    The idea is two torsion boxes, connected by four V-rail beams.
    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
    [assembled.scad, configuration.scad, connectors.scad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]
2016-03-22 Added test parts, working on the end plates
    Need to orient the support beams vertically... so that you can recover
    lost nuts!
    [beam.scad, connectors.scad, endcap.scad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]
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2016-03-24 Test array for the laser cutter.
    Looks like kerf of -.2 is the best :-)
    [connectors.scad, test_array.dxf]
2016-03-29 Finished all the plates!
    Ready to cut!
    Not really... I need to do the housekeeping of getting each plate to lie
    flat and get projected so I can output a DXF. But it's close :-)
    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
    [configuration.scad, endcap.scad]
2016-03-30 DXF-ified
    Added DXFs for all the bits; minor changes to the plates.
    [bottom_wall.dxf, connectors.scad, cross_plate.dxf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]
2016-03-31 Shrank the support walls a bit
    I'd like to cut some of the material out, but the long planes are nice
    and strong... I think this design is ready for a test.
    The dxf's are moved, but not updated. I need to make a script to
    generate 'em from the command line.
    [bottom_wall.dxf, cross_plate.dxf, end_plate.dxf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]
2016-04-01 Finally added a bit of a batch file to spit out the endcap dxf's automagically.
    [bottom_wall_plate.dxf, configuration.scad, connectors.scad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]
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2016-04-05 Working on the gantry, and trying to figure out how much extra room I need around the bed.
    Hoping to shrink the printer size, without shrinking the print size :-)
    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
    [configuration.scad, endcap.scad, gantry.scad]
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2016-04-06 Shrank the end plates, and added a test plate
    End plates are now 420mm on a side; this gives you 40mm on either side
    of the gantry to switch nozzles/move it about. This might not be
    enough.
    [bottom_wall.dxf, bottom_wall_plate.dxf, configuration.scad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]
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2016-04-08 Working on the gantry. Would like to shrink it a bit more.
    Main missing part: belt tensioner.
    - Thinking about making the motors slot-mounted, and making a printed part to pull on 'em for tensioning.
    - - maybe add a hole for the idler in the support plate - so you can crank it back nice and far.
    It needs a long tensioner, to account for belt stretch :-)
    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
    [configuration.scad, endcap.scad, gantry.scad]
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2016-04-21 Modifying the gantry
    This commit is between prints - want to offset the gantry wheels further before printing them again.
    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
    [gantry.scad, gantry_carriage.stl, gantry_clamp.stl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]
2016-04-22 More work on the gantry.
    Need to fix up the belt path behind the gantry ends. The two-part end isn't very stable, I don't think it's viable.
    [configuration.scad, endcap.scad, gantry.scad]
2016-04-24 Redesigned the gantry carrier - moved motors to accommodate.
    Redesign means the gantry beam needs to be cut with precision... but the previous design was unfixably sloppy.
    Now need two gantry carriages and one hotend carriage to build the printer.
    [bottom_wall_plate.dxf, configuration.scad, end_plate.dxf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]
2016-04-25 Changed the end plate to corners
    Trying to make the design easier to build, smaller, but still rigid.
    Now the support plate is solid, but only the corners are reinforced.
    Todo: move the Z motors to the top... to match the other motors, and to
    give better support to the single motor side.
    Todo: Add mounting holes for the various electronics bits.
    [bottom_wall_plate.dxf, configuration.scad, corner_plate.dxf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]
2016-04-25 Moved the Z motors to the top bars
    Should provide better support. Plus it means the printer doesn't need
    tall feet... although I didn't adjust the feet at all.
    [bottom_wall_plate.dxf, endcap.scad, top_wall_plate_idler.dxf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]
2016-04-25 Added an idler
    I neglected to add the second idler for the belt crossover... whoops.
    Luckily I didn't cut before noticing.
    A todo is to move the crossover inside the endcap, but for the first
    build I'd rather have it out where I can keep an eye on it... and figure
    out how to actually build it.
    [endcap.scad, top_wall_plate_idler.dxf]
2016-04-25 Updated the YZ dimensions to give more room front to back - needed for the gantry.
    [bottom_wall_plate.dxf, configuration.scad, corner_plate.dxf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]
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2016-04-27 Added the cut plate
    just a plate to mount four 2040 beams to so you can cut all of them at once, to the exact same length.
    Actual length gan be fudged a little, but if they're not the same you'll be really sad.
    Estimates, pre-assembly:
    500mm for a single doppelbot
    800mm for a double doppelbot
    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
    [drill_plate.dxf, drill_plate.scad]
2016-04-28 Added tabs to the end plates, and center mount for the support plate
    The center of the wall plates was a bit wobbly for my taste. Of course, that was with only the corners attached - but still.
    Moved the Z stage inwards a couple mm - I really need my m8 flanged bearings to come in so I can mount the Z screws and see how that's going to work.
    My guess is I'll add a couple small pincher screws to clamp the flanged bearings in.
    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
    [bottom_wall_plate.dxf, configuration.scad, connectors.scad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]
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2016-05-11 Fixed the top brace - bad coding - and added the cut plate to laser out the bed.
    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
    [bed.scad, bed_brace_top.dxf, cut_plate.dxf]
2016-05-13 Messed up the inside and outside holes :-(
    Old ones didn't line up with the beam.
    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
    [bed.scad, bed_inside.dxf, bed_outside.dxf]
2016-05-17 Adjusted the Z leadscrew sticky-outy.
    Because it didn't sticky-outy enough :-(
    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
    [bed.scad, configuration.scad]
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2016-05-17 Adjusted the top and bottom wall plate distance
    Converted the plates and gantry ends to use smaller idlers.
    Next todo is fix belt tensioning on the hotend carriage.
    [bottom_wall_plate.dxf, configuration.scad, endcap.scad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]
2016-05-18 Gantry ends are done.
    And printed! With the beam hugger, you don't need exact length beam across.
    Next step, the hotend carriage needs a full redesign.
    - maybe design it as belt tensioner carriage with hotend mounting?
    [gantry.scad, gantry_carriage.stl, gantry_clamp.stl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]
2016-05-18 Bumped out the end plates, better clearance on the lead screws
    placement toying with the gantry, nothing really set yet.
    [bottom_wall_plate.dxf, endcap.scad, gantry.scad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]
2016-05-23 Belt tensioner in place.
    Uses two idler assemblies, and a stretcher with a fixed peg.
    The intent is that you use one LONG belt, run it through the tensioner and tighten both belts at once.
    Then, drop a zip tie around the belt, to make sure that one half of the belt doesn't stretch more than the other half.
    The zip tie should fix the carriage around the center point, cutting down on cross-gantry loading.
    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
    [belt_stretcher.stl, configuration.scad, gantry.scad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]
2016-05-23 Gantry mods.
    Also changed the m5 screw rad - it didn't have slop calculated in. Probably need to recalculate the M5 holes in the MDF sections.
    [belt_stretcher.stl, configuration.scad, gantry.scad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]
2016-05-26 Gantry tensioner complete!
    Need to make a hotend mount - it'll just re-use the four screwholes for the belt attachment and v-wheels, stiffening the carriage, too.
    First model accepts the e3d Chimaera, it'll be upgradable to the Kraken.
    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
    [belt_stretcher.stl, gantry.scad, gantry_carriage.stl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]
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2016-05-31 Fixed up the hotend mount :-)
    Need to add some zip tie holes so I can secure the wires.
    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
    [gantry.scad, hotend_mount.stl]
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2016-06-13 Fixed up the extruders, added some bed clips.
    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
    [bed.scad, bed_brace_top.dxf, bed_clamp.stl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]
2016-06-22 Set of updates
    The gantry restricts flow too much - so have to expand it :-)
    Also added some extras for MakerFaire.
    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
    [PanelDueEnclosure.scad, PanelDueEnclosure.stl, PanelDueMirror.stl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]
2016-06-25 Adjusted sizing - thicker endcaps, and wider. Extra space around the carriage, so it's not so tight.
    Also added mounting holes for electronics.
    TODO: test cut the narrower M5 guides in the frame
    TODO: Make an AC cover, that mounts the power switch & makes it impossible to touch the business end of the relays and power supply connectors.
    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
    [bed_brace_top.dxf, bed_clamp.stl, bed_end_top.dxf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]
2016-06-26 Reworked the bed braces, finished mounting the power supply cover.
    I think it's good to go :-) Next step is to work up a layout for the laser cutter.
    [bed.scad, bed_brace_top.dxf, bed_clamp.stl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]
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2016-07-07 Fixed the endcap cuts - it was missing the belt slots!
    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
    [bottom_wall_plate.dxf, end_plate.dxf, endcap.scad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]
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2017-02-12 Added flanges to connect smooth rods to the bed
    The leadscrews aren't stiff enough... not even close!
    Using LM10UU flanged bearings to attach to 10mm smooth rods.
    [bed.scad, bed_brace_top.dxf, bed_clamp.stl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]
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2017-02-14 Updating the original bed.
    Some of the dimensions changed - these files shouldn't be needed. I reverted to the new dimensions as well.
    [bed.scad, old_outside.dxf, old_top.dxf]
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2017-02-23 Finished converting gantries to plastic spring
    The offset nuts didn't sit well enough, led to lots of vibration.
    Need to fix up the hotend carriage rear - 2 part maybe? And the belt stretcher could use an update.
    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
    [bed.scad, bed_clamp.stl, belt_stretcher.stl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]
2017-02-26 Updated gantry & carriages
    Using print-in-place plastic springs instead of offset cam nuts. The nuts kept coming loose... not sure if I was using them incorrectly or what.
    Springs appear to be more robust, but only printed with them briefly.
    [belt_stretcher.stl, belt_stretcher_3.stl, gantry.scad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]
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2017-04-13 Updating machine frame, shortening it to accommodate the leadscrews.
    [bottom_wall_plate.dxf, bottom_wall_support_plate_.dxf, configuration.scad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]
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2017-04-19 The corner supports were too long!
    [bottom_wall_plate.dxf, bottom_wall_support_plate_.dxf, corner_plate.dxf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]
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2017-04-21 Swapped out the metric frame nuts for English.
    English nuts are bigger... although now I wonder if metric coarse
    thread nuts are also big.
    In any case, the rails are held in by self-tapping torx drive
    screws, and the frame is held together by the same T-25 Torx head.
    [bed_brace_top.dxf, bed_clamp.stl, bed_end_top.dxf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]
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2017-05-05 Added ablity to stiffen the endcaps with embedded 2020 beams.
    [beam.scad, configuration.scad, endcap.scad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]
2017-05-05 Fixed the beam holes on the top and bottom
    Lasercut files have NOT been generated!
    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
    [endcap.scad]
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2017-05-08 Changing up the belt mounting.
    New plan:
    two slots on the front of the vertical gantry, belt goes in on the beam side, around the area between the slots and back on itself.
    Slits in the rear vertical gantry for zip ties, to lock it onto the belt. Maybe a better, more permanent lock?
    single slot on the back side of the vertical gantry, belt passes through it and then into a clamp, with a screw tightener facing the front.
    Belt tension procedure:
    loosen rear vertical gantry belt clamp
    tighten/adjust vertical gantry tensioner
    square the axis against the frame
    tighten rear vertical gantry belt clamp
    [configuration.scad, gantry.scad]
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2017-06-16 Strengthened the belt tensioner clamp.
    [belt_tensioner_clamp.stl, gantry.scad]
2017-06-16 Updated the belt double clamp - it was a smidge loose.
    [belt_double_clamp.stl, gantry.scad]
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2017-07-17 Fixed the outside bed bits
    [bed.scad, bed_clamp.stl, bed_end_top.dxf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]
2017-07-26 Updated bed files, added an untested bed clamp.
    In particular, I think the clamp top is too thin - which needs to
    match the thickness of the bed plastic, so ideally as thin as it
    can get - hence the test.
    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
    [bed.scad, bed_clamp.stl, bed_double_end_top.dxf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]
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2017-08-08 Removed cap recesses from the belt separator - they were on the wrong side :-P
    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
    [belt_separator.scad, belt_separator.stl]
2017-08-09 playing with the gantry... the Aero doesn't fit anywhere easily.
    [gantry.scad, gantry_extruder.scad]
2017-08-11 Updated the extruder carriage
    New mount includes the Aero attachment built-in; should be much
    stiffer. Also includes mounts for the height sensor and cable
    chain, as well as improved belt attachment.
    Now, the tensioner is on the rear carriage, which retains its
    grooved attachment mount (might come in handy someday?). Front
    belt is attached with two zip ties, which can easily slide on.
    Printing now - untested STLs.
    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
    [configuration.scad, functions.scad, gantry.scad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]
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2017-10-25 Updated the extruder for a Bowden.
    Height is approximate... and probably not correct.
    [bowden_carriage.stl, extruder_e3d_bowden_mount.stl, extruder_mount.scad]
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
